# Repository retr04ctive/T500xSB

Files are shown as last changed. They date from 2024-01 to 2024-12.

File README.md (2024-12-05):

# T500xSB Printhead Retroactive Remix

Remix of the T500xVoron mod created by Trist0ne



## Acknowledgements

**Huge thanks for all of the foundation work here:**

 - [T500xVORON](https://github.com/Trist0ne/T500xVORON)

 Follow his method for everything, substuting parts as shown below to fit your needs.

## Features

* Nozzle: [Bambu Hotend](https://www.amazon.com/dp/B0C8JZ788Y/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)
* Thermister and Heater: [Bambu Heater](https://www.amazon.com/dp/B0BW3WXVNR/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)
* Extruder: [Bondtech LGX Lite 2](https://a.co/d/76f52Fn)
* Printhead control board: [BigtreeTech SB2209 RP2040](https://biqu.equipment/products/bigtreetech-ebb-sb2209-can-v1-0)
* Printer control board: [SKR 3 EZ Control Board 32bit](https://www.amazon.com/dp/B0B1WQ9B8L/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)
* Printhead display board: [BigtreeTech KNOMI V2](https://biqu.equipment/products/bigtreetech-knomi-v1-0?_pos=1&_psq=knomi&_ss=e&_v=1.0&variant=40556258459746)
* Buildplate: [WhamBam PEX](https://www.whambamsystems.com/products/flexi-plate-with-pre-installed-pex-build-surface-510-x-510-creality-cr-10-s5_)
* LED Lighting: [RAINBOW BARF LED TOOLHEAD HARNESS FOR STEALTH BURNER](https://kb-3d.com/store/printer-specific-harnesses/566-rainbow-barf-led-toolhead-harness-for-stealth-burner-1653783045189.html)
* Heatbed Mosfet: [MKS MOSFET MOS Module](https://a.co/d/cuV4RM1)

## Modified Printed parts list

**THESE MUST ALL BE PRINTED FROM ABS OR ASA. THEY ARE DESIGNED FOR ABS, I USED ASA. OTHER MATERIALS ARE NOT SUITABLE EITHER DUE TO THEIR TEMPERATURE RESISTANCE OR STRUCTURE CREEP OVER TIME; YOU HAVE BEEN WARNED**

* [STL files](https://github.com/retr04ctive/T500xSB/tree/primary/STL)

## Config file changes

To run this project, you will need to change the Kliper config files to the ones in the config folder above.

I also installed a [Logitech C920 USB Webcam](https://www.logitech.com/en-ch/products/webcams/c920-pro-hd-webcam.960-001055.html) to use with [Obico](https://www.obico.io/) for spaghetti detection.

[Raspberry Pi Pico ADXL](https://klipper.discourse.group/t/raspberry-pi-pico-adxl345-portable-resonance-measurement/1757)

## Recommendations

Follow the [Ellis' Print Tuning Guide](https://ellis3dp.com/Print-Tuning-Guide/articles/index_tuning.html) as well as running the calibrations in [Orca Slicer](https://github.com/SoftFever/OrcaSlicer/wiki/Calibration)

[Sensorless Homing](https://docs.vorondesign.com/community/howto/clee/sensorless_xy_homing.html)

[Klipper PID Tunuing](https://www.obico.io/blog/klipper-pid-tuning/)

[Input Shaping](https://www.klipper3d.org/Measuring_Resonances.html#bed-slinger-printers)

[Perssure Advance](https://github.com/SoftFever/OrcaSlicer/wiki/Calibration)

Slicer Configuration
* Edit your printer settings "Machine G-code" tab as follows:
  * PRINT_START EXTRUDER=[nozzle_temperature_initial_layer] BED=[bed_temperature_initial_layer_single] CHAMBER=[chamber_temperature]
  * PRINT_END

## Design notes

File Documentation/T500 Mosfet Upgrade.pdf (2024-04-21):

## T500 Mosfet Upgrade

I do not recommend doing this unless your warranty has expired

### Prerequisites

Hardware:
Amazon 30a Mosfet https://www.amazon.com/gp/product/B08YZ4W4LN or
Big Red https://www.amazon.com/gp/product/B074KZF772)

STL Files:
1x Mosfet Adapter https://www.thingiverse.com/thing:6375709

Mosfet Install
- Follow this video to remove your mosfet
https://fb.watch/oX4d6himoZ/
- Take the 4 screws from the mosfet and install the Mosfet adapter you printed above
- Take 2 or 4 Screws and install your mosfet to the adapter plate
- Plug the 2 wire control into the board
- Install the 2 wires that come from the PS into the POWER of the New Board (See Diagrams Below)
- Plug to 2 Wires from the Bed Heater into the HOT BED connections (See Diagrams Below)

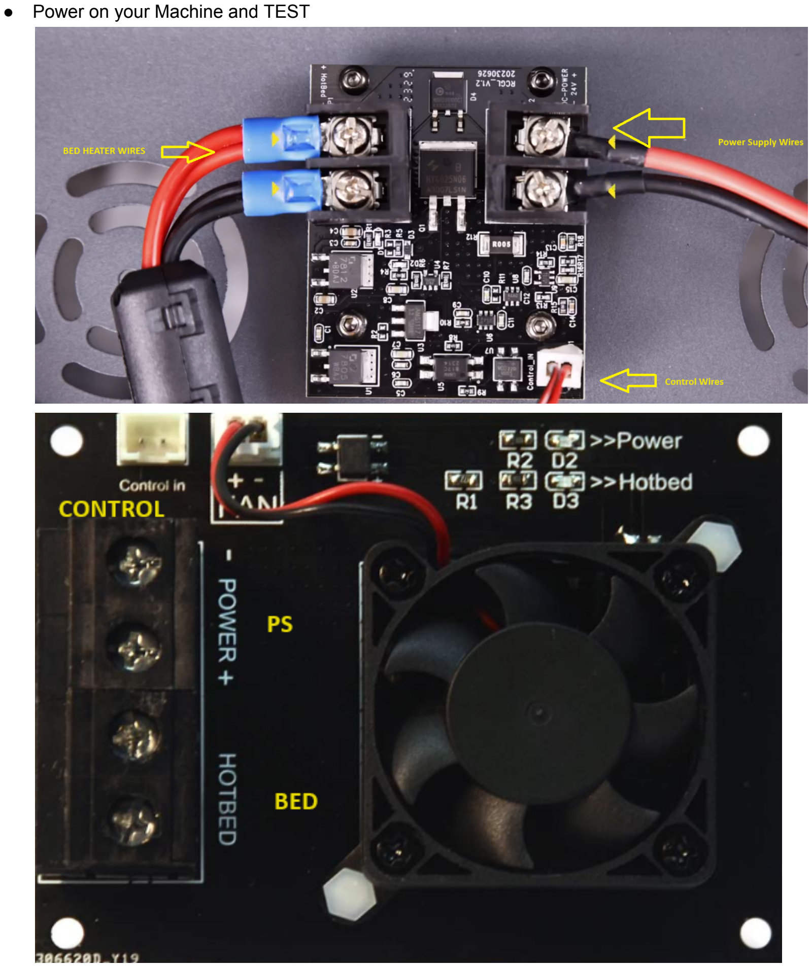
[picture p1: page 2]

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
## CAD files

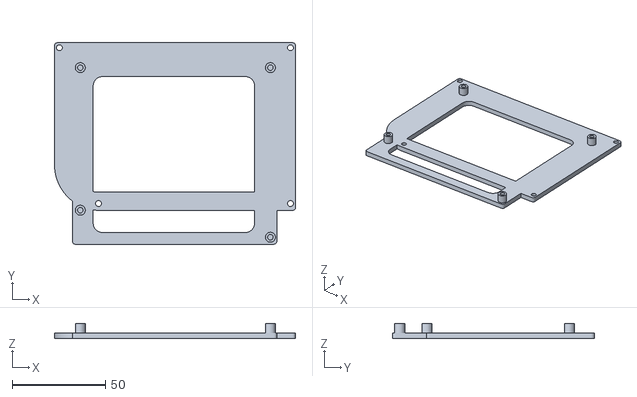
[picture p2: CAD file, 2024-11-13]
STL/SKR T500 Mount.stl
129.3 x 108.1 x 8.00

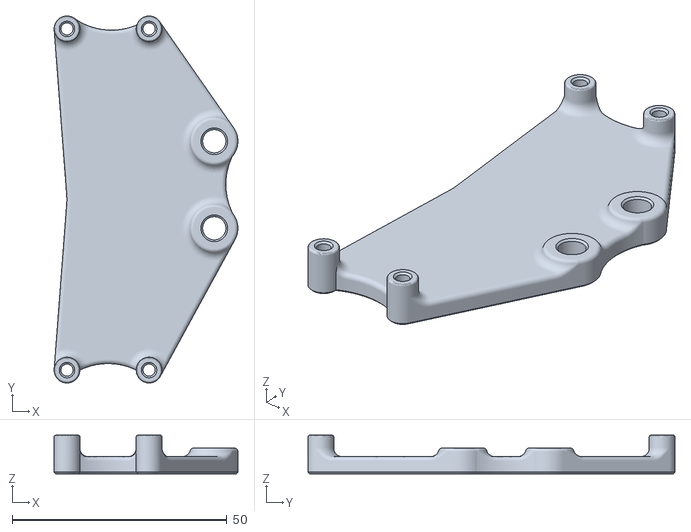
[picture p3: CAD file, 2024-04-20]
STL/BTT U2C Mount.stl
42.8 x 85.4 x 9.00

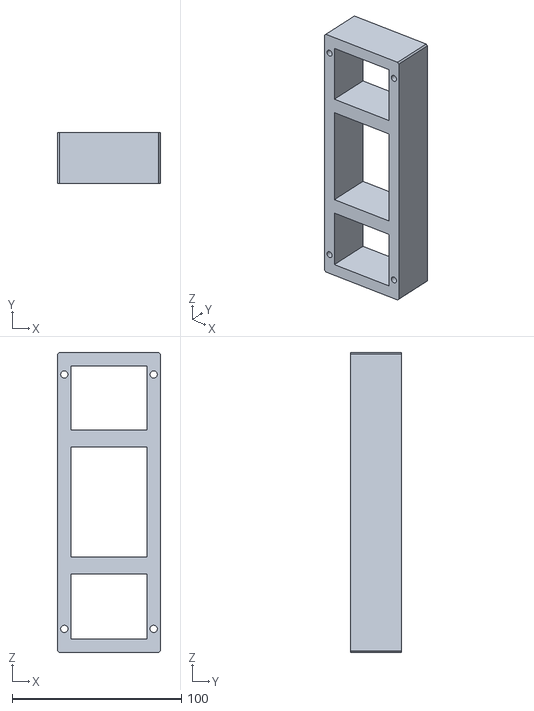
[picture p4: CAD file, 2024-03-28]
STL/Bed Spacer T500 v3.stl
60.9 x 30.0 x 177.5

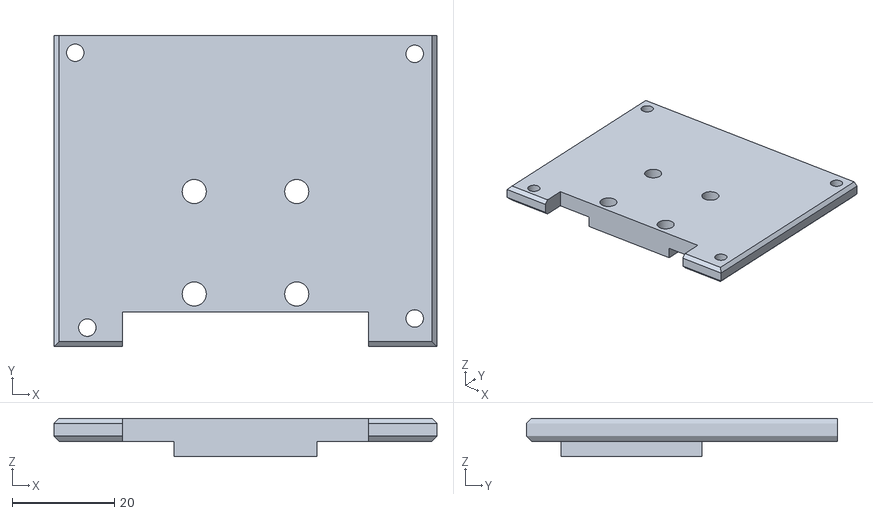
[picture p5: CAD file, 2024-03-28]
STL/Toolhead Adapter Plate.stl
74.8 x 60.7 x 7.50

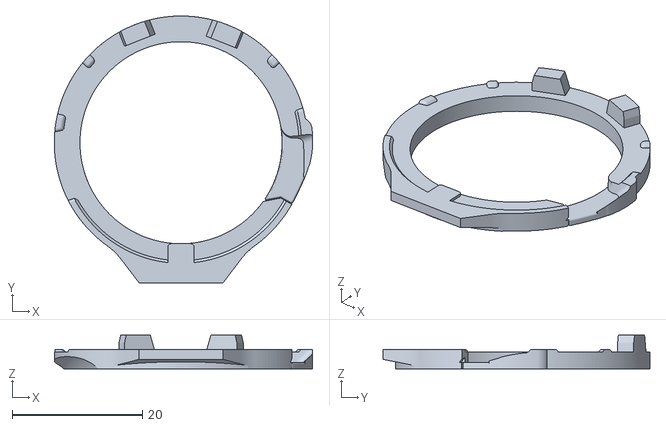
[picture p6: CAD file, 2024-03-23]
STL/KNOMI 2 Mounting Plate.stl
39.7 x 41.0 x 5.20

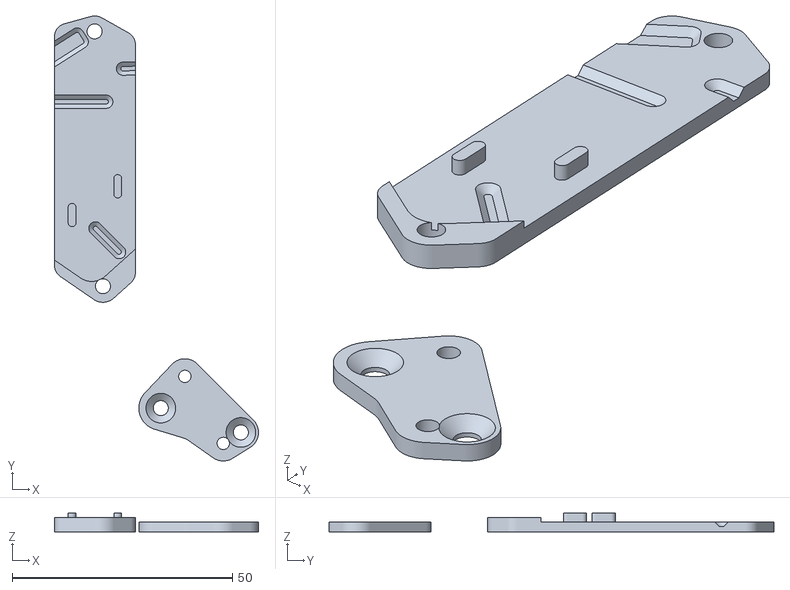
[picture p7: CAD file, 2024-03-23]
STL/ebb_brackets.stl
46.3 x 101.1 x 4.21

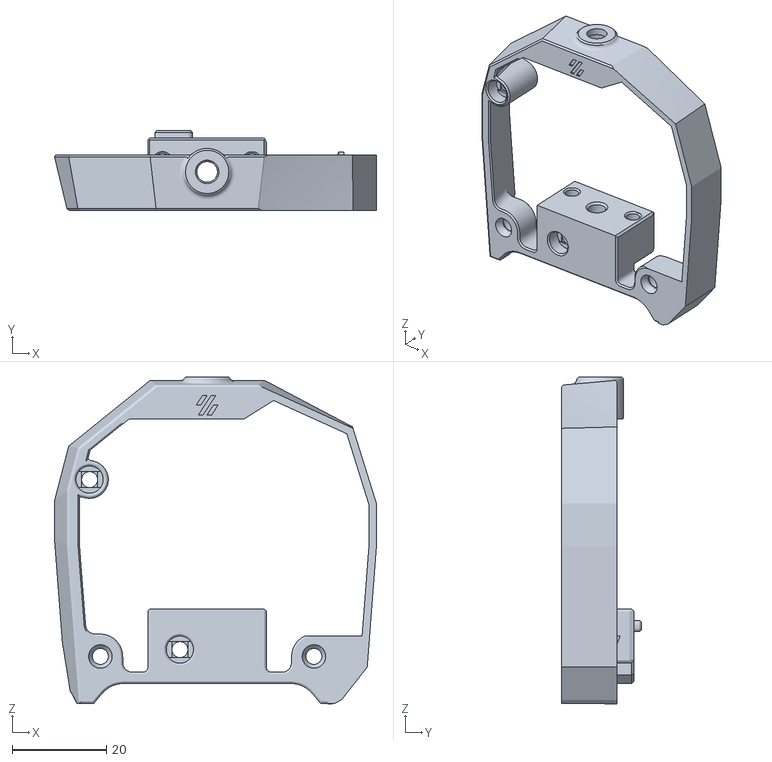
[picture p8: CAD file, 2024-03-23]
STL/LGX_Pro_Front_v1.stl
68.5 x 17.0 x 69.5

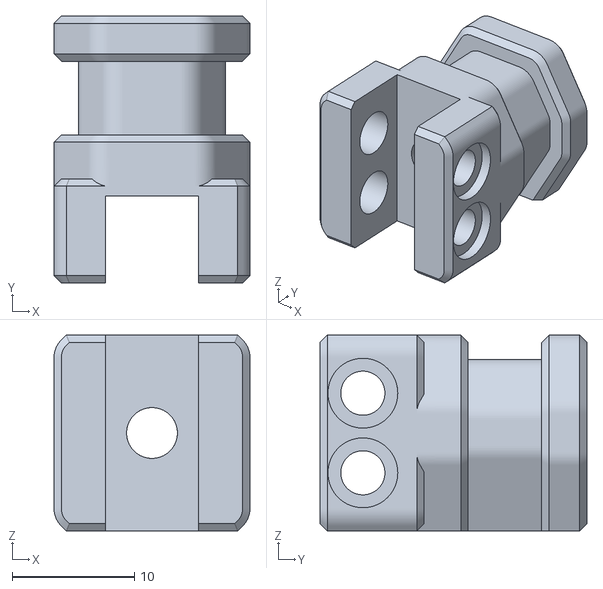
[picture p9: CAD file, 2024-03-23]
STL/SB Bambu Hotend Insert.stl
16.0 x 21.8 x 16.0

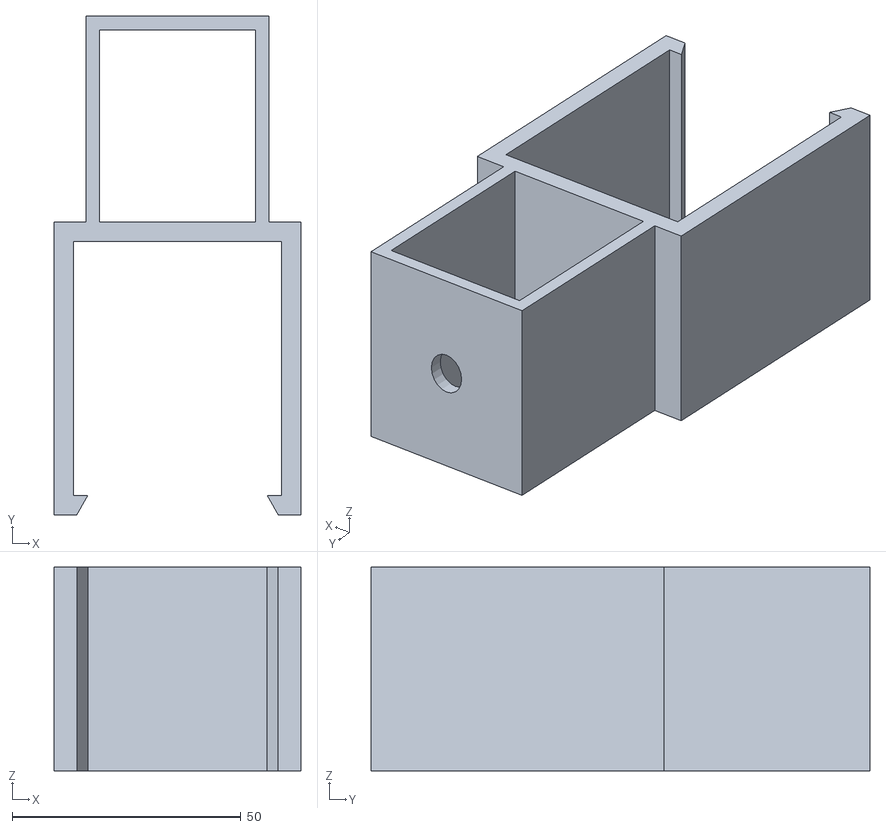
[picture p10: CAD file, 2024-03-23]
STL/Comgrow_t500_cam_mount.stl
54.0 x 109.0 x 44.5

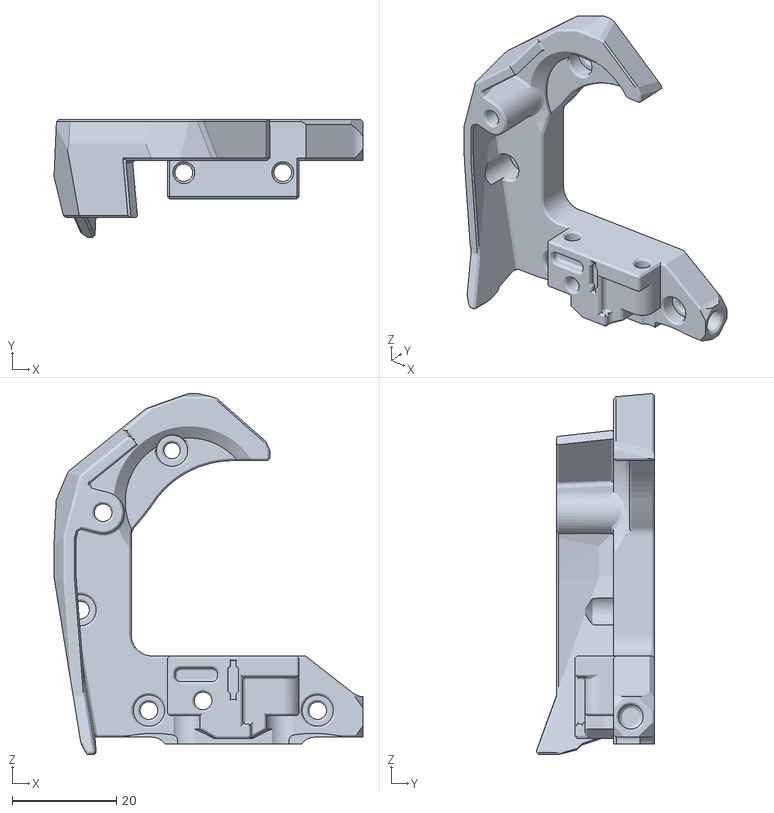
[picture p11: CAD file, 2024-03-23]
STL/LGX_Pro_back_v2.stl
59.3 x 22.6 x 69.3

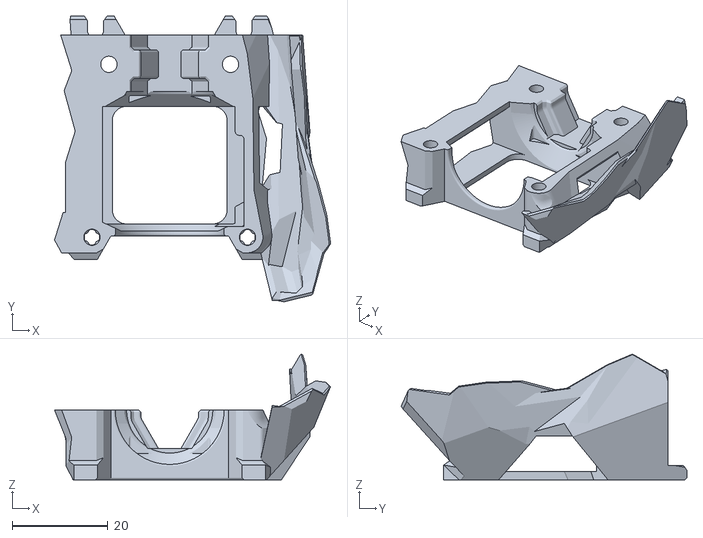
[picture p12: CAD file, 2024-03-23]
STL/SB Bambu Hotend Back.stl
57.7 x 59.7 x 26.3

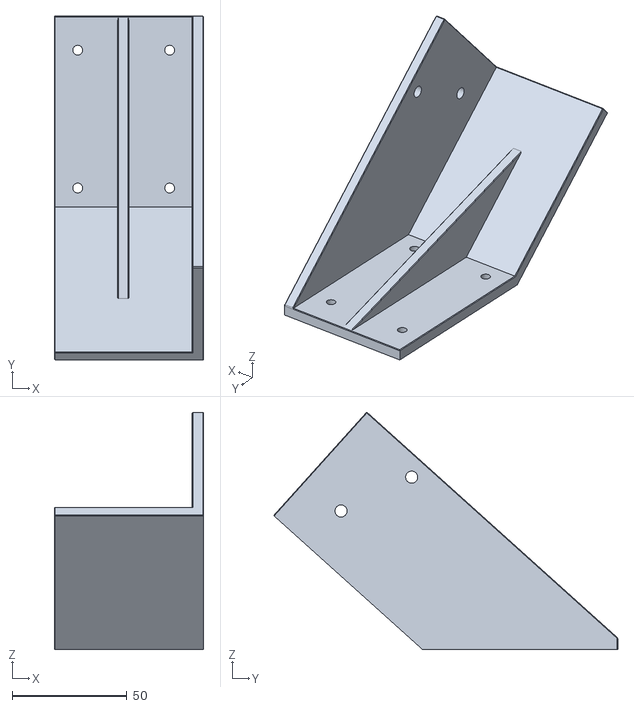
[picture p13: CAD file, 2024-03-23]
STL/Pi TFT70 BTT Case_Bracket_v2.stl
65.0 x 149.6 x 103.1

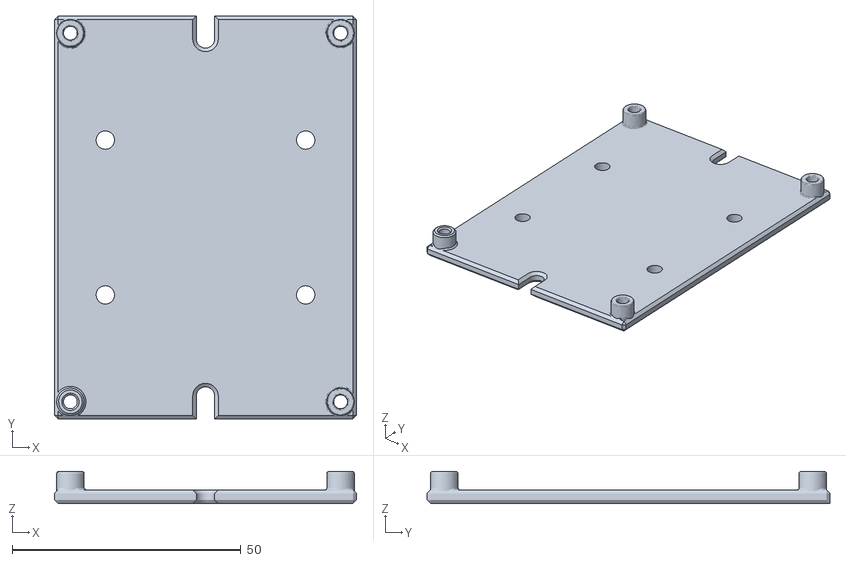
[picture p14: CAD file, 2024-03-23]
STL/T500_MOSFET_ADAPTER_3.stl
66.0 x 88.0 x 7.00

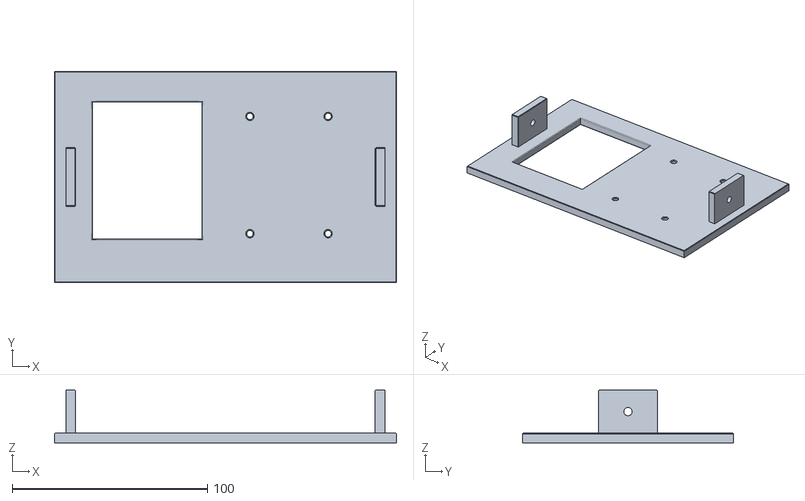
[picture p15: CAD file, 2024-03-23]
STL/Pi TFT70 BTT Case_Back_v4.stl
175.0 x 108.0 x 27.0

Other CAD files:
STL/Comgrow_t500_BTT_SFS_Mount.stl
STL/adxl345_bed_clamp-t500.stl

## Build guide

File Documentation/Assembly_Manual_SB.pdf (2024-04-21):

1

## VORONDESIGN.COM

## VERSION 2023-07-07

# VORON STEALTHBURNER

## We build space shuttles with gardening tools

so anyone can have a space shuttle of their own.

# VORON

2

## VORONDESIGN.COM INTRODUCTION

Before you begin on your journey, a word of caution.

In the comfort of your own home you are about to assemble a robot. This machine can maim, burn, and electrocute you if you are not careful. Please do not become
the first VORON fatality. There is no special Reddit flair for that.

Please, read the entire manual before you start assembly. As you begin wrenching, please check our Discord channels for any tips and questions that may halt your progress.

Most of all, good luck!
THE VORON TEAM

3

## VORONDESIGN.COM TABLE OF CONTENTS

## Introduction

## Hardware

## Overview

## ClockWork2

## Tool Cartridge

## StealthBurner

## X Carriage

## ADXL Mount

## Next Steps

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
## VORONDESIGN.COM INTRODUCTION

PART PRINTING GUIDELINES
The Voron Team has provided the following print guidelines for you to follow in order to have the best chance at success with your parts. There are often questions about substituting materials or changing printing standards, but we recommend you follow these:

3D PRINTING PROCESS
Fused Deposition Modeling (FDM)

MATERIAL
ABS

LAYER HEIGHT
Recommended: 0.2mm

EXTRUSION WIDTH
Recommended: Forced 0.4mm

INFILL TYPE
Grid, Gyroid, Honeycomb, Triangle or Cubic

INFILL PERCENTAGE
Recommended: 40%

WALL COUNT
Recommended: 4

SOLID TOP/BOTTOM LAYERS
Recommended: 5

PRINT IT FORWARD (PIF)
Often times community members that have issues printing ABS will bootstrap themselves into a VORON using our Print It Forward program. This is a service where approved members with VORON printers can make you a functional set of parts to get your own machine up and running. Check Discord if you have any interest in having someone help you out.

5

## VORONDESIGN.COM

HOW TO GET HELP
If you need assistance with your build, we’re here to help. Head on over to our Discord group and post your questions. This is our primary medium to help VORON Users and we have a great community that can help you out if you get stuck.

## https://discord.gg/voron

PRIMARY COLOUR

Example z_joint_lower_x4.stl
These files will have nothing at the start of the filename.

ACCENT COLOUR

Example [a]_tensioner_left.stl
We have added “[a]” to the front of any STL file that is intended to be printed with accent color. The parts are marked with a heart in the manual.

QUANTITY REQUIRED

Example [a]_z_belt_clip_lower_x4.stl
If any file ends with “_x#”, that is telling you the quantity of that part required to build the machine.

FILE NAMING
By this time you should have already downloaded our STL files from the Voron GitHub. You might have noticed that we have used a unique naming convention for the files. This is how to use them.

## INTRODUCTION

CLEAR/TRANSPARENT

Example [c]_led_diffuser.stl
We have added “[c]” to the front of any STL file that is intended to be printed with clear or transparent filament (cloudy is better than clear; white or light grey may also work in a pinch).

OPAQUE

Example [o]_led_diffuser_mask.stl
We have added “[o]” to the front of any STL file that is intended to be printed with an opaque filament (blocks light, dark colours and blacks).

6

## VORONDESIGN.COM INTRODUCTION

THIS IS JUST A REFERENCE
This manual is designed to be a simple reference manual. Building a Voron can be a complex endeavour and for that reason we recommend downloading the CAD files off our Github repository if there are sections you need clarification on. It can sometimes be easier to follow along when you have the
whole assembly in front of you.

## https://github.com/vorondesign

## https://docs.vorondesign.com

REPORTING ISSUES
Should you find an issue in the documentation or have a suggestion for an improvement please consider opening an issue on GitHub (https://github.com/VoronDesign/Voron-Stealthburner/issues). When raising an issue please include the relevant page numbers and a short description; annotated screenshots are also very welcome. We periodically update the manual based on the feedback we get.

# DOCS (https://docs.vorondesign.com/)

7

## VORONDESIGN.COM

BUTTON HEAD CAP SCREW (BHCS) Metric fastener with a domed shape head and hex drive. Most commonly found in locations where M5 fasteners are used.

ISO 7380-1

SOCKET HEAD CAP SCREW (SHCS) Metric fastener with a cylindrical head and hex drive. The most common fastener used on the Voron.

ISO 4762

## HARDWARE REFERENCE

SELF TAPPING SCREW
Fastener with a pronounced thread profile that is screwed directly into plastic.

HEAT SET INSERT
Heat inserts with a soldering tip so that

they melt the plastic when installed. As the plastic cools, it solidifies around the knurls and ridges on the insert for excellent resistance to both torque and pull-out.

WASHER
Usually stamped from sheet metal this

type of spacer is not as consistent in thickness as the shims are. Only used in M3 size.

DIN 125

SET SCREW
Small headless screw with an internal drive. Used in pulleys and other gears. Also called a grub screw.

ISO 4026

HEX NUT
Hex nuts couple with bolts to create a tight, secure joint.

ISO 4032

FLAT HEAD CAP SCREW (FHCS) Metric fastener with a flat head and hex drive.
ISO 10642

8

## VORONDESIGN.COM

## VORONDESIGN.COM

## OVERVIEW

9

Voron StealthBurner

Voron ClockWork2 Extruder

Voron StealthBurner Tool Cartridge

ADXL Sensor Mount

10

VORON CLOCKWORK2 | VORONDESIGN.COM

11

## VORONDESIGN.COM

Heat Set Insert

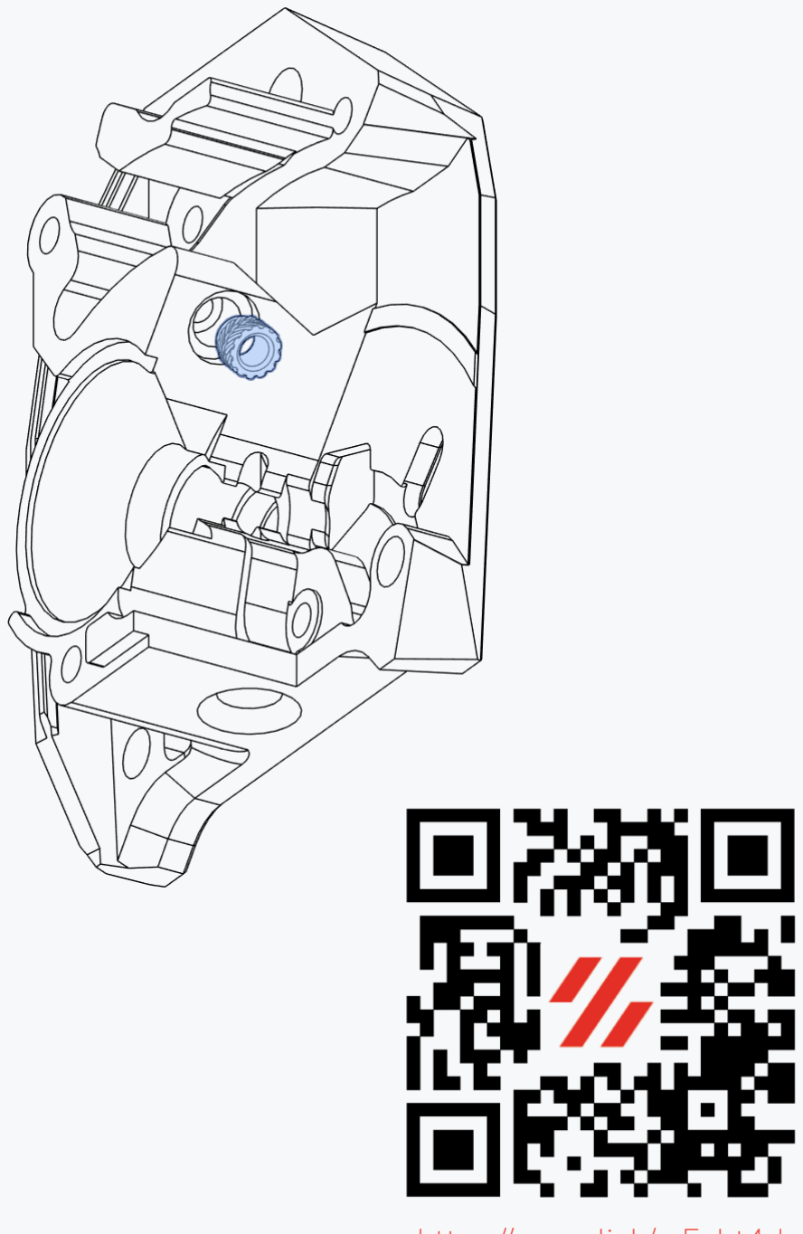
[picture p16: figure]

https://voron.link/m5ybt4d

HEAT SET INSERTS
This design relies heavily on heat set inserts. Make sure you have the proper inserts (check the hardware reference for a close-up picture and the Sourcing Guide (https://vorondesign.com/sourcing_guide) for dimensions).

If you’ve never worked with heat set inserts before we recommend you watch the linked guide.

## HEAT SET INSERTS

## VORONDESIGN.COM

## HEAT SET INSERTS

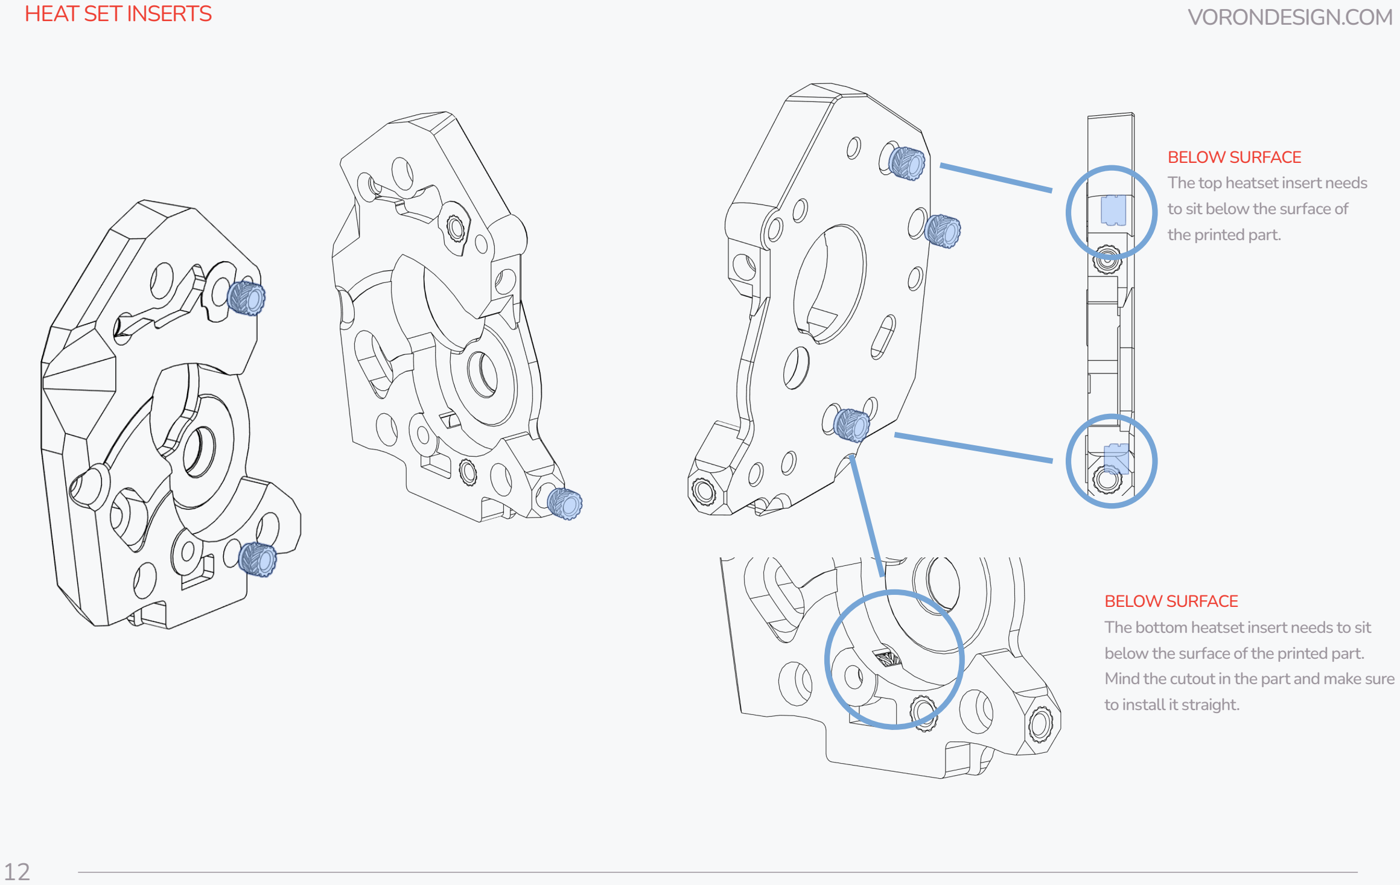
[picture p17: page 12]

12

BELOW SURFACE
The bottom heatset insert needs to sit below the surface of the printed part. Mind the cutout in the part and make sure to install it straight.

BELOW SURFACE
The top heatset insert needs to sit below the surface of the printed part.

13

## VORONDESIGN.COM

OPTION: TOOLHEAD PCB
If you opt to use a toolhead PCB, add additional heat set inserts into locations highlighted below.

Heat Set Insert

## HEAT SET INSERTS

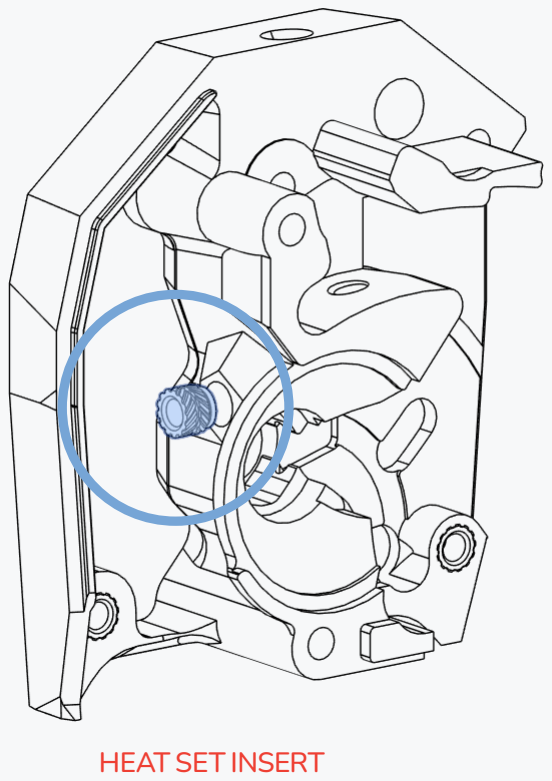
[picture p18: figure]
HEAT SET INSERT

Be careful when inserting this heat set insert. It’s easy to accidentally touch the left side of the part with the soldering iron.

14

## VORONDESIGN.COM

GENERIC CABLE CHAINS
The 3-hole pattern is usually found on generic cable chains.

IGUS CABLE CHAINS
IGUS chains have 2 mounting holes.

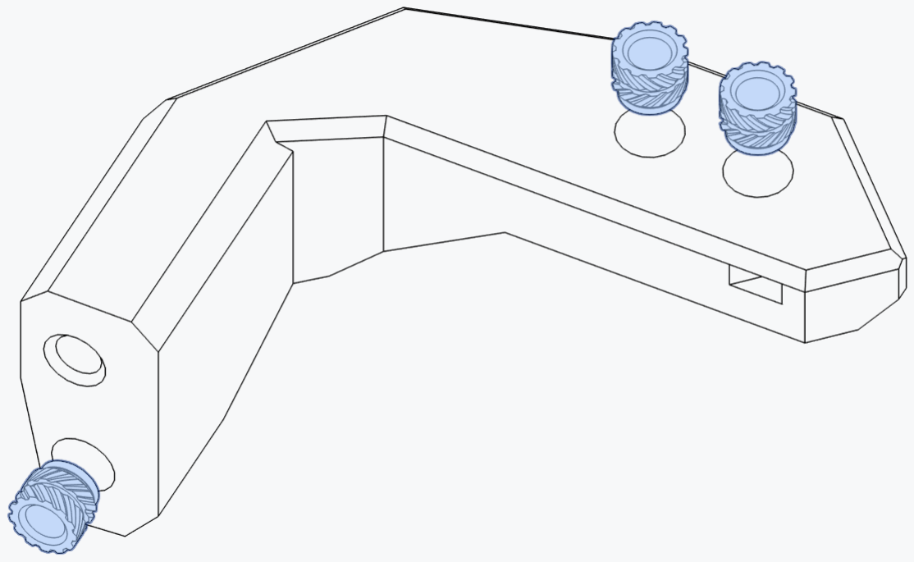
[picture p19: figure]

Heat Set Insert

## HEAT SET INSERTS

PRINTER SPECIFIC MOUNTS
V2, Trident and Legacy use the same printed parts. Extra parts are included for SwitchWire.

15

HEAT SET INSERTS | VORONDESIGN.COM

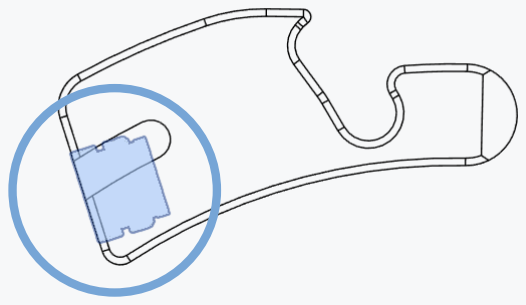
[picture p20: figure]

FLUSH WITH SURFACE
The heatset insert needs to sit flush or slightly below the surface of the printed part.

ACCENT PART?
Look for Voron heart next to the part. It indicates that this is a part that is usually printed in the accent color.

16

GUIDLER ARM | VORONDESIGN.COM

GUIDLER ARM | VORONDESIGN.COM

17

BMG Idler Assembly

LUBRICATE BEARINGS
A lubrication film is required to ensure smooth operation and longevity.
Refer to the Voron sourcing guide (https://vorondesign.com/sourcing_guide) for lubricant options - look for a “light grease”.

MIND ORIENTATION
Make sure to orient the idler assembly as shown above.

## VORONDESIGN.COM

## GUIDLER ARM

18

BMG Thumbscrew Assembly

A NOTE ON SPRINGS
Longer/shorter/stiffer springs will change the tension characteristics and have an impact on how well the tension mechanism works. Consider buying the original Bondtech part (https://www.bondtech.se/product/thumbscrew-assembly/) as those are known to work well. If sourced from a different vendor check if it’s roughly 12mm long with an outer diameter of 6mm and a wire thickness of 1mm.

19

## VORONDESIGN.COM

MR85 Bearing

## MOTOR PLATE

BEARING FIT

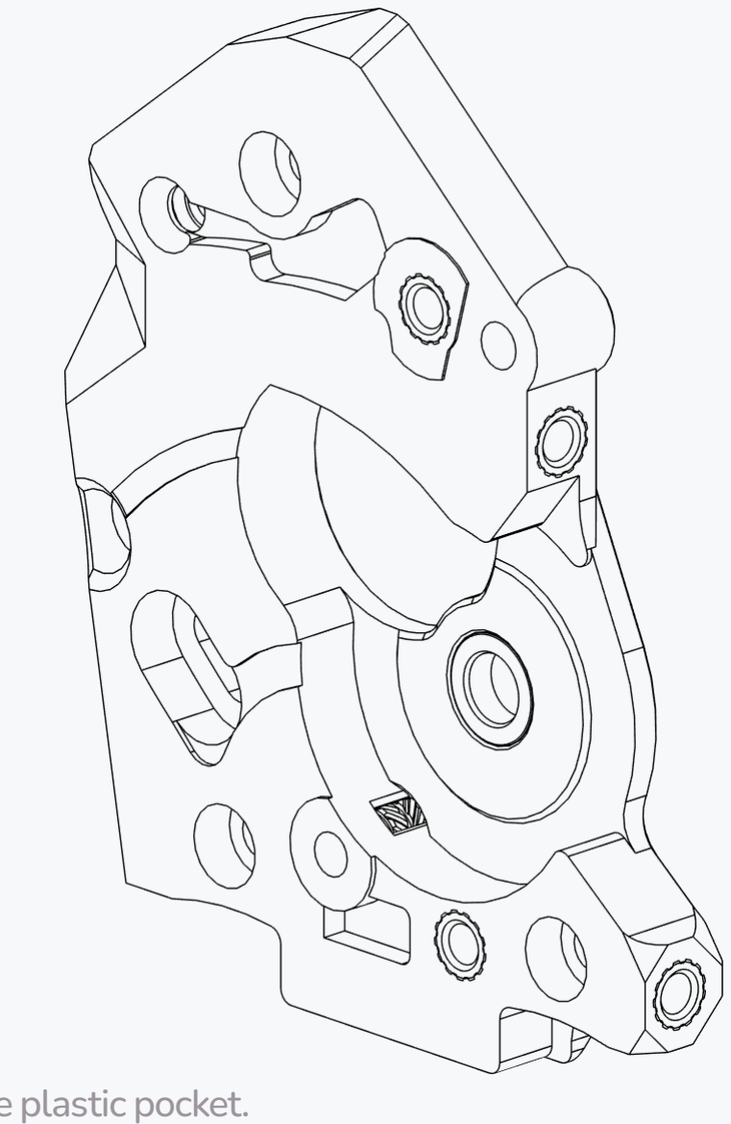
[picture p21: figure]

Fully seat the bearing into the plastic pocket. Apply even pressure to insert them. Avoid pressing on the inner ring of the bearing.

If the fit is too tight the printed parts are likely over-extruded.

MR85 Bearing

CHECK BEARING FIT
The bearings must slip on and off the shaft easily to allow the gear to self-centre.

Pressing the bearings on the shaft will damage them.

Lightly sand the shaft if required.

20

## VORONDESIGN.COM

MR85 Bearing

## MAIN BODY

M3x6 FHCS

BEARING FIT
Fully seat the bearing into the plastic pocket. Apply even pressure to insert them. Avoid pressing on the inner ring of the bearing.

THREAD LOCKER PLEASE
Adding a small amount of medium strength thread locker to this flat head screw will keep it from coming loose over time.

21

## VORONDESIGN.COM

DRIVE GEAR
Make sure the set screw in the filament drive gear is seated against the notch in the shaft. Carefully tighten the set screw, the head is easy to strip.

## DRIVE ASSEMBLY

A NOTE ON GEARS
Poorly made gears often cause print quality issues. For best performance consider

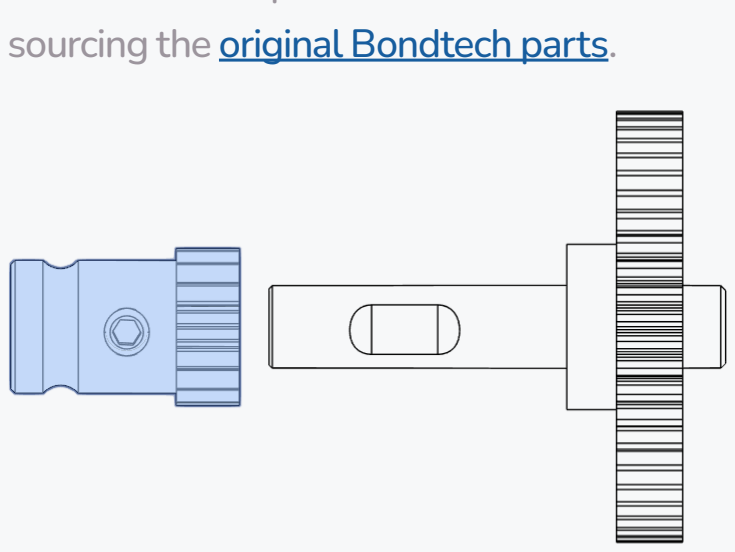
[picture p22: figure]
sourcing the original Bondtech parts.

INITIAL POSITION

The final position is set later.

The final position of the drive gear is set in a later step. Common thread lockers have a long enough working time to complete the steps without issues.

Familiarize yourself with the steps on the next 3 pages before you apply thread locker.

Complete the steps on the next 3 pages after applying the thread locker.

22

MAIN BODY | VORONDESIGN.COM

23

## VORONDESIGN.COM

M3x25 SHCS

INITIAL ALIGNMENT CHECK
Check if the filament path aligns with the toothed section of the drive gear.

## MAIN BODY

Tighten until the plastic bends and cracks. Back up 2 turns, discard parts, reprint and try again.

24

## VORONDESIGN.COM

CHECK FOR CLEARANCE
The drive shaft must not touch the motor housing. Make sure it does not sit above the surface of the printed part.

Check if the shaft has sufficient clearance when fully seated.

Depending on the shafts tolerances you may need to adjust the position of the drive gear or sand the face of shaft.

CHECK ALIGNMENT
With the filament inserted, verify if the filament path and drive gear are aligned.

Loosen the set screw and adjust the position of the drive gear if required.

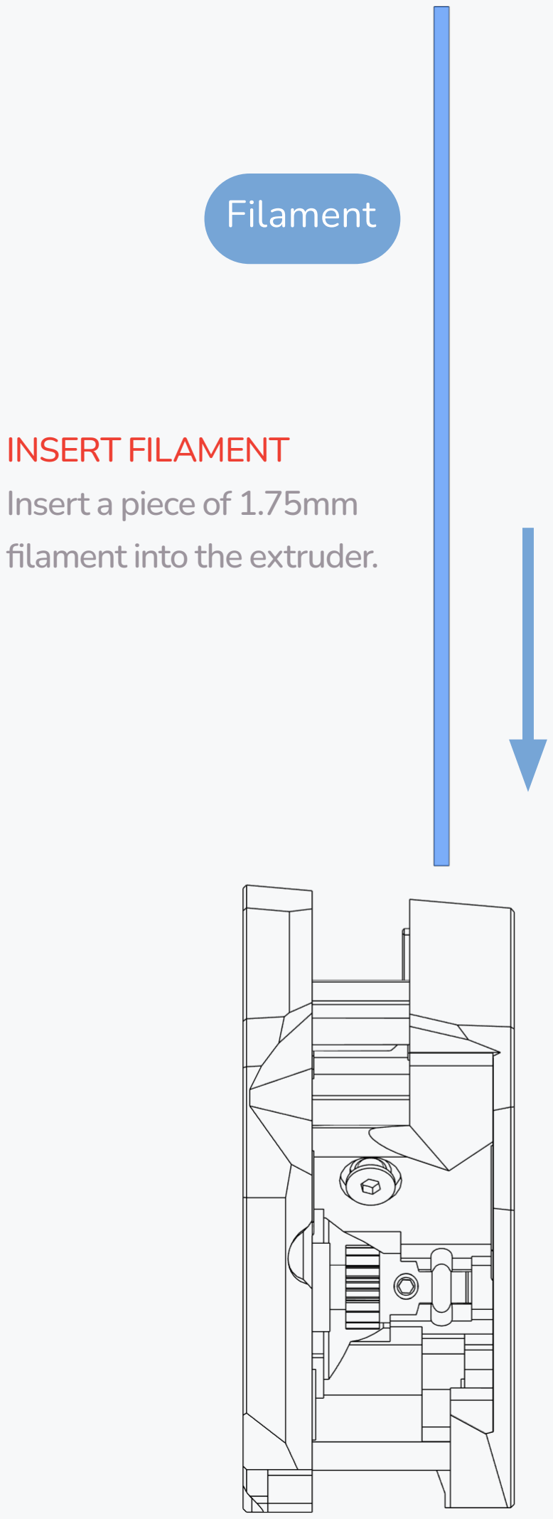
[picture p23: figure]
Insert a piece of 1.75mm filament into the extruder.; Filament

INSERT FILAMENT

## DRIVE ALIGNMENT

TENSION ARM | VORONDESIGN.COM

25

M3x25 SHCS

DON’T TIGHTEN
The tensioning arm must move freely. Tightening the bolt may lock it in place.

26

## VORONDESIGN.COM

M3x25 SHCS

## LATCH

27

TENSION MECHANSIM | VORONDESIGN.COM

TENSION KNOB
Turning the thumb screw clockwise will increase the tension and grip on the filament. Too much tension will result in print issues.

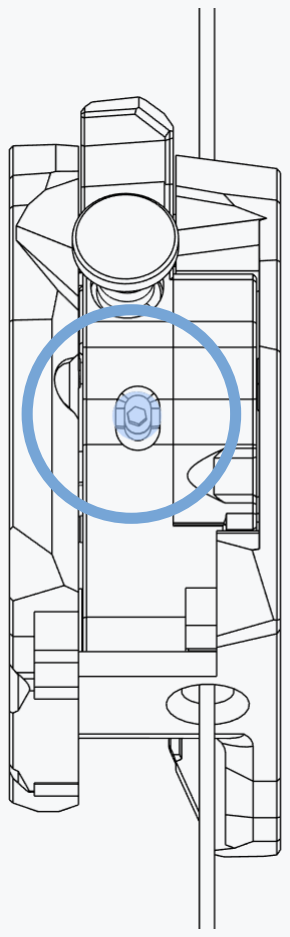
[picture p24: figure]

ANTI SQUISH THINGYMAJIG
Softer and flexible materials will deform
and extrude poorly under too much tension. ClockWork2 adds an adjustment feature to set the minimum distance between the drive gear and the idler, limiting the squish on the filament, and to prevent the gears from meshing too tightly or binding up the extruder.

## VORONDESIGN.COM

## STEPPER MOTOR

28

M3x30 SHCS

NEMA14 Stepper

29

## VORONDESIGN.COM

M3x8 SHCS

ACCESS HOLE

The second motor bolt can
be accessed from the front of the extruder.

## STEPPER MOTOR

The motor position will be adjusted in the next steps. Don’t fully tighten just yet.

30

## VORONDESIGN.COM

CHECK GEAR PLAY
The gear should have a slight play and should not be fully tight against the pinion. Adjust the position of the motor until you have a faint play.

SET GEAR MESHING
Adjust the stepper motor position so that the motor and extruder gear teeth fully mesh /overlap with each other. There should be a very small gap between the faces of the gear teeth; the gears must not press tightly against each other.

## STEPPER MOTOR

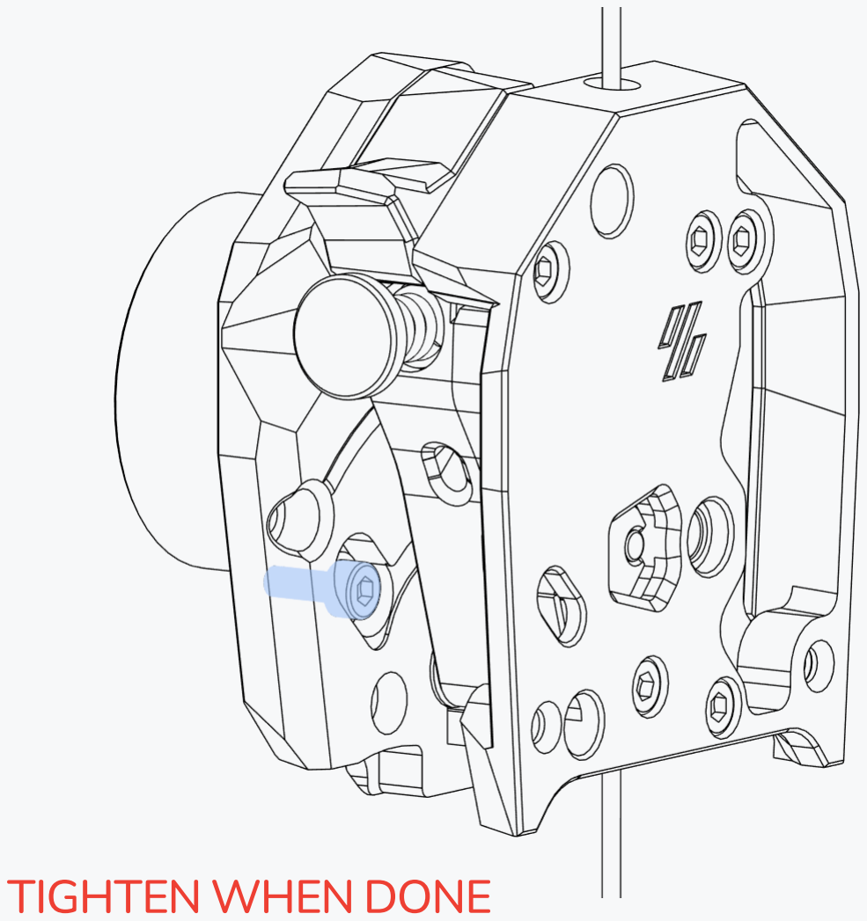
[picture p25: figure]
TIGHTEN WHEN DONE

Don’t forget to tighten the second motor bolt after adjusting.

https://voron.link/u6ehxsw

31

CHAIN ANCHOR | VORONDESIGN.COM

32

CABLE BRIDGE | VORONDESIGN.COM

M3x8 SHCS

CABLE COVER | VORONDESIGN.COM

33

M3x16 SHCS

OPEN LATCH
Undo the filament latch to expose the bolt pocket for the cable cover.

## VORONDESIGN.COM

## CABLE COVER

34

ACCESS HOLE
The bolt drive can be accessed from the front of the extruder.

DON’T OVER-TIGHTEN
The bolt is threaded directly into plastic.

M3x6 BHCS

35

## VORONDESIGN.COM

StealthBurner development started on 2021-04-13 with a simple: “I’m going to regret saying this but, ‘How hard could it be?’”

36

## VORONDESIGN.COM

37

## VORONDESIGN.COM

IDENTIFYING PRINTED PARTS
The hotend type is embossed on the printed parts.

Make sure they match your hotend.

AVAILABLE MOUNTS

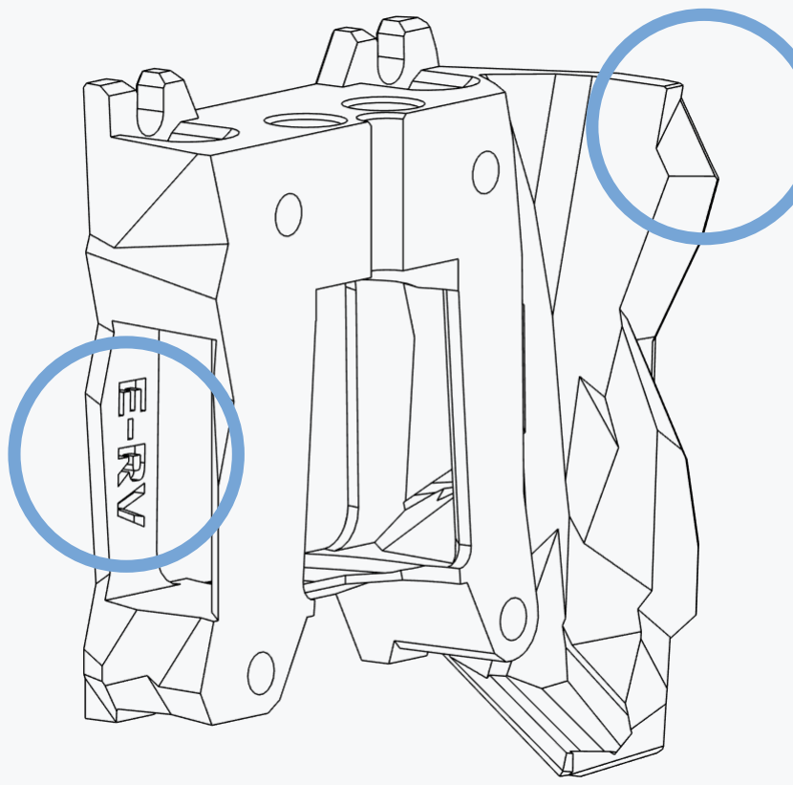
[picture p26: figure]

We also provide mounts for other hotends. They are assembled in a similar manner.

For a full list of available mounts and their identification code, see the readme file included in the toolheads folder.

## PART MARKINGS

MISSING CORNER? CW1? CW2?
We also provide tool cartridge parts for ClockWork1, and other extruders designed as an alternative to CW1. They are identical except for an opening in the highlighted corner to help with wire routing for those designs.

38

## VORONDESIGN.COM

OPTION: ADXL PCB MOUNT
To use the optional ADXL PCB for Klipper’s Input Shaper calibration, add additional heat set inserts into the holes in highlighted location.

Heat Set Insert

## PART PREP

39

## VORONDESIGN.COM

Revo Nozzle

Revo HeaterCore

Revo Voron Heatsink

## PART PREP

40

PART PREP | VORONDESIGN.COM

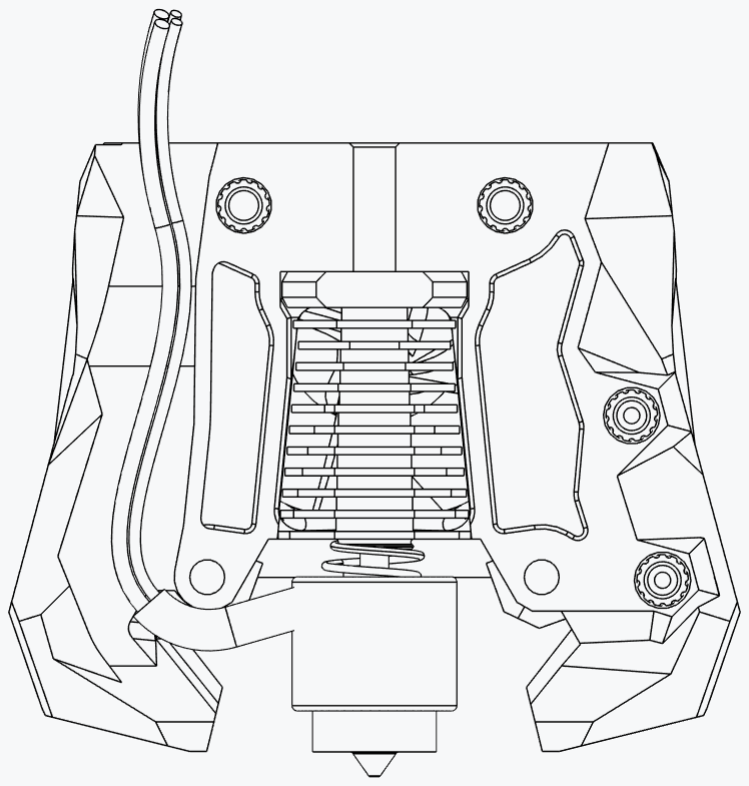
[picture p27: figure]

BEND STRAIN RELIEF
Carefully bend the strain relief to clear the printed part. Firmly hold the HeaterCore to prevent bending the Revo Nozzle.

It is critical that the Revo Nozzle is fully hand tightened into the heatsink. You MUST bend the strain relief to achieve this.

HOTEND WIRE ROUTING
Route the wires as shown to the right. This is universal to all hotend types.

41

## VORONDESIGN.COM

M3x16 SHCS

## TOOL CARTRIDGE

42

## VORONDESIGN.COM

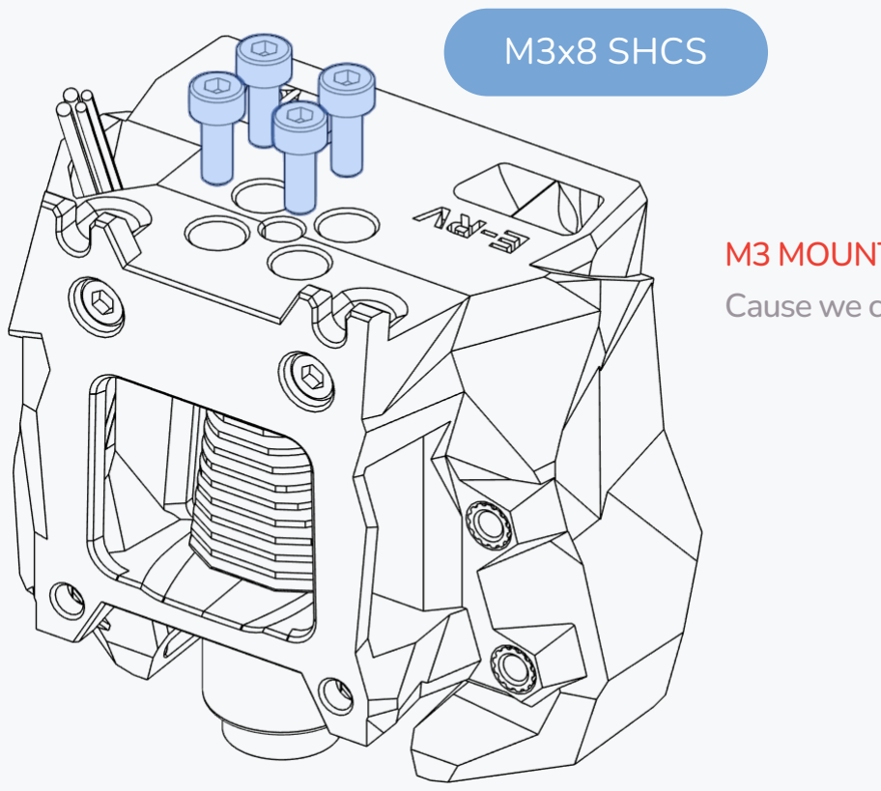
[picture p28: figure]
M3x8 SHCS

M3 MOUNTING BOLTS?
Cause we can, that’s why.

## TOOL CARTRIDGE

43

## VORONDESIGN.COM

PTFE STICKOUT
The PTFE tube should stick out 11mm above the surface of the printed part.

The stick out length might vary if you use an extruder other than the ClockWork2.

## TOOL CARTRIDGE

44

## VORONDESIGN.COM

45

## VORONDESIGN.COM

Remove built-in supports (highlighted in

## SUPPORTS

## VORONDESIGN.COM

46

DOUT

DOUT

DOUT
DIN

DIN

DIN | DIN

### DOUT

5V

GND

5V

5V

GND

GND

To Controller Board

+ -

120mm 3x 0.16mm²(AWG26-30)

100mm 3x 0.16mm²(AWG26-30)

LOGO LED
Index=1

TOOLHEAD LED RIGHT
Index=2

TOOLHEAD LED LEFT
Index=3

100mm 3x 0.16mm²(AWG26-30)

### DIN

### DOUT

5V

GND

### DIN

### DOUT

5V

GND

To Controller Board

LED WIRING
Connect the “OUT” side of the LED to the “IN” side of the next LED in the chain.

Solder the wires as shown on the right. Both the “IN” and the “OUT” wires must exit in the same direction in order to fit into the printed parts.

For Illustration Only, Read “LED Wiring” Callout

47

LEDS | VORONDESIGN.COM

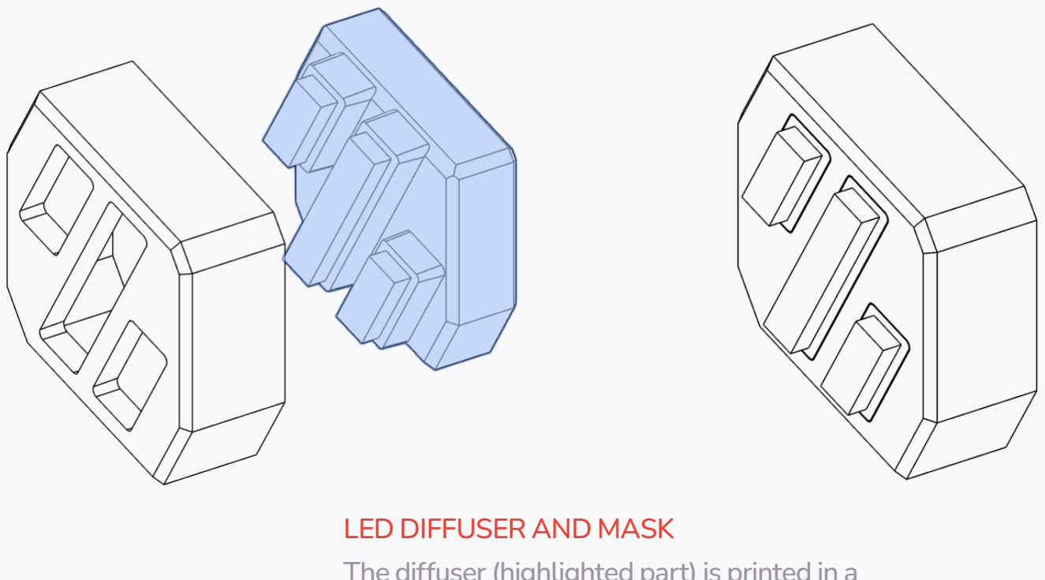
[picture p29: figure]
LED DIFFUSER AND MASK

The diffuser (highlighted part) is printed in a translucent filament to evenly spread the light.

The mask (part to the left) is printed in an opaque filament to prevent the light from leaking, resulting in a crisp logo.

48

LEDS | VORONDESIGN.COM
TOOLHEAD LED LEFT | TOOLHEAD LED RIGHT

49

LEDS | VORONDESIGN.COM

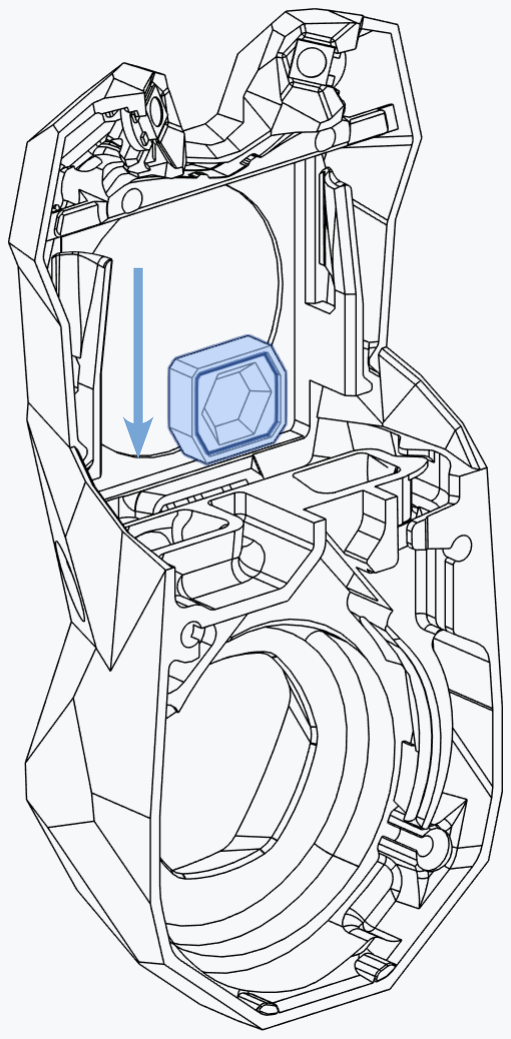
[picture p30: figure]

DIFFUSER INSERTION
Insert the printed parts and push them towards the front.

50

LEDS | VORONDESIGN.COM

51

## VORONDESIGN.COM

## LEDS

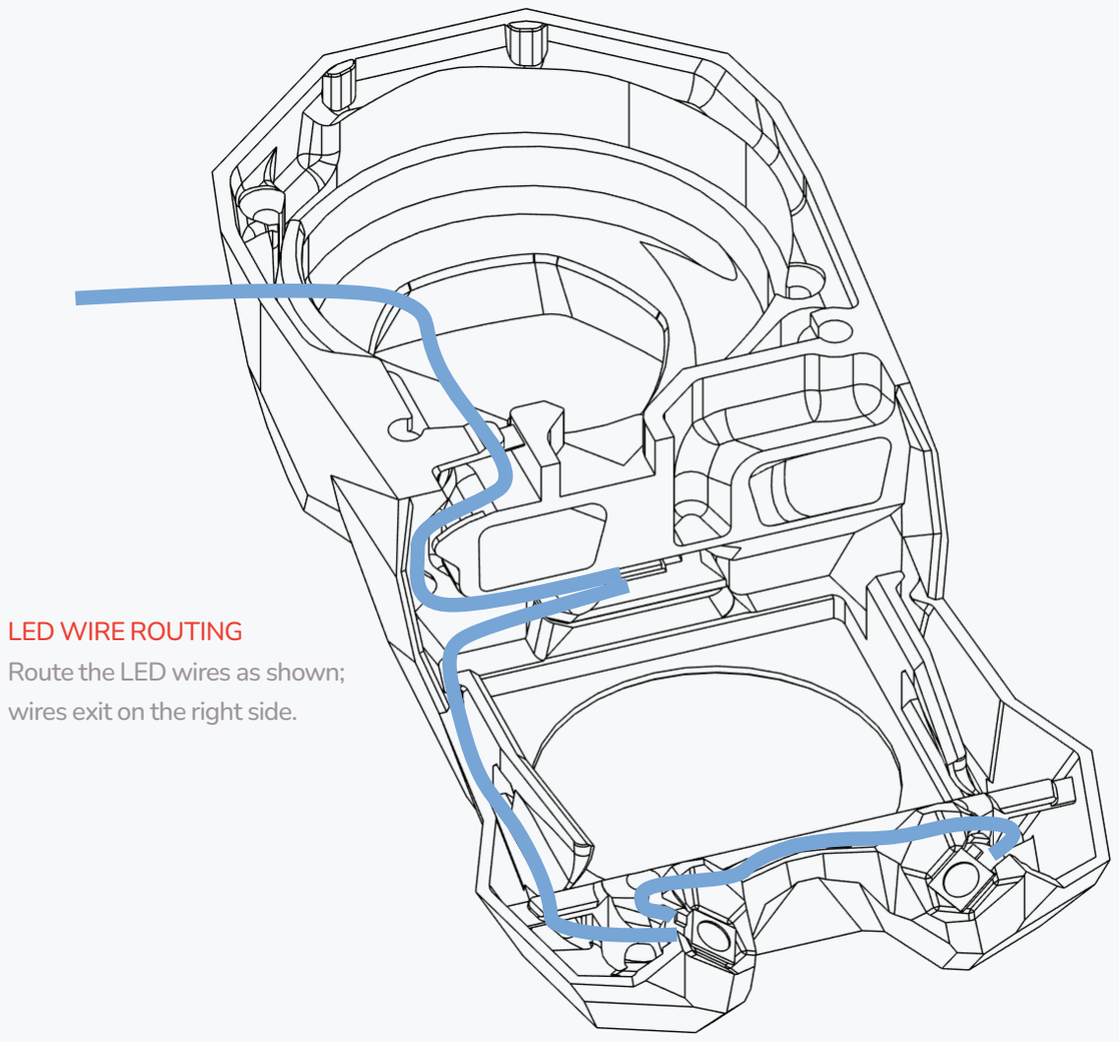
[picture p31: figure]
LED WIRE ROUTING Route the LED wires as shown; wires exit on the right side.

52

## VORONDESIGN.COM

The highlighted parts are build-in support

during the fan installation.

## SUPPORTS

53

## VORONDESIGN.COM

Rotate the fan so that the wires exit on the top and the air is pushed “inwards”.

## HOTEND FAN

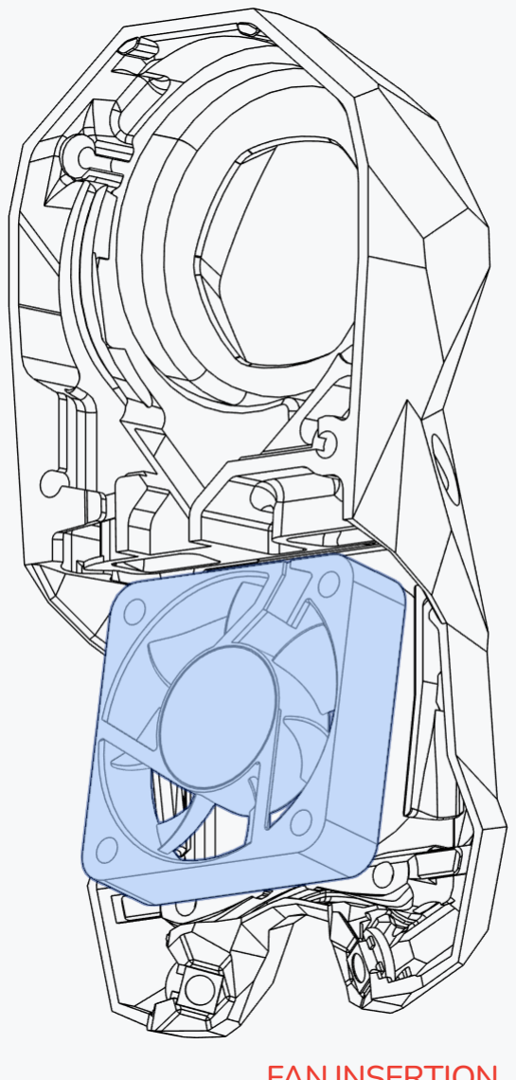
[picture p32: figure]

FAN INSERTION

Insert the fan at a slight angle and clip it into place.

Mind the fan orientation.

54

HOTEND FAN | VORONDESIGN.COM

FAN WIRE ROUTING

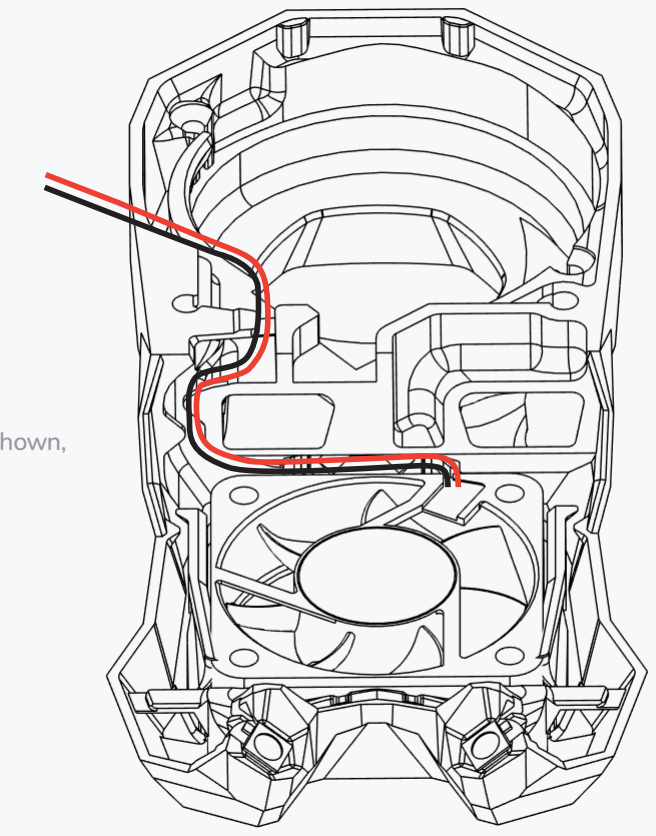
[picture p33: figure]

Route the fan wires as shown, exiting on the right side

55

## VORONDESIGN.COM

FAN PREPARATION
Remove the front of the 5015 fan. Clip off and file down the stock mounting ears.

There’s a trimming jig STL included in the release to make this task easier.

## PART COOLING FAN

56

PART COOLING FAN | VORONDESIGN.COM

M3x6 FHCS

57

## VORONDESIGN.COM

Yeah, it went about as expected.

58

X CARRIAGE | VORONDESIGN.COM

59

## VORONDESIGN.COM

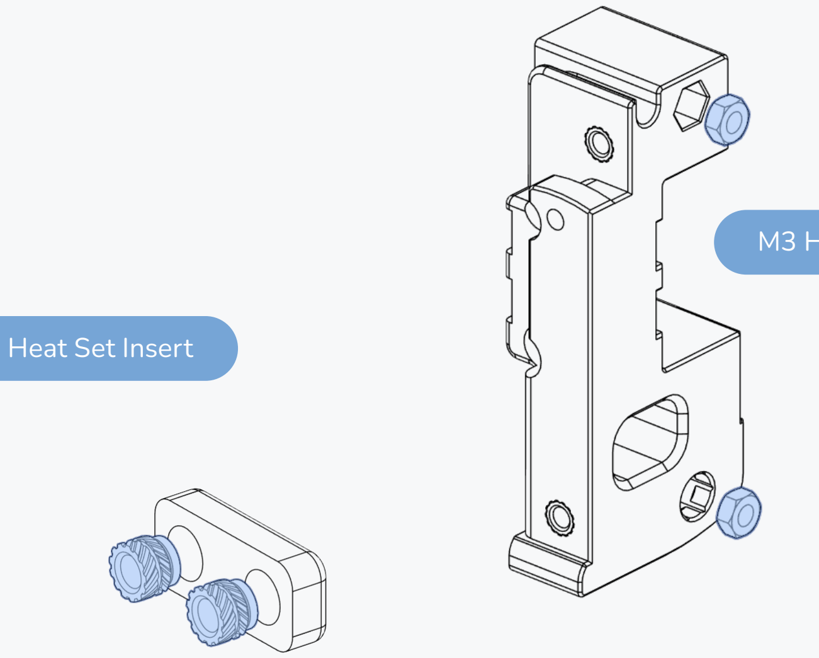
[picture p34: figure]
Heat Set Insert

M3 Hex Nut

## PART PREP

We provide different versions of the carriage to fit our different printer designs. Be sure to pick the right one for your printer. the next few pages may look slightly different if you are building a Switchwire printer.

60

## VORONDESIGN.COM

## X CARRIAGE

FOLLOW BELTING AND X CARRIAGE INSTALLATION OUTLINED IN PRINTER MANUAL Consult the printer’s manual for instructions on how to run the belts and details on carriage mounting.

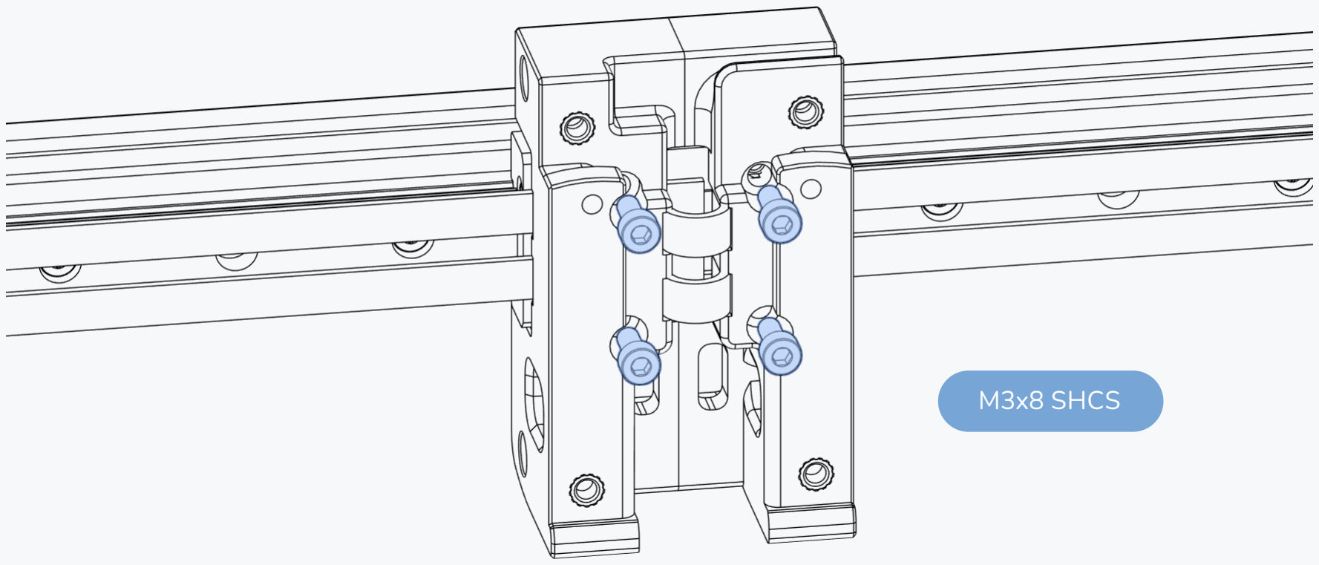
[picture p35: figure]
M3x8 SHCS

## VORONDESIGN.COM

## X CARRIAGE

61

M3x30 SHCS

M3x30 SHCS

M3x12 SHCS

30MM OR 40MM?
the length of these two bolts can be different based on the specific printer you are building. This step has some overlap with the printer manuals. please refer to the printer psecific manual for the correct bolt lengths

## VORONDESIGN.COM

## X CARRIAGE

62

Omron Style Probe | M3x30 SHCS

OTHER PROBE TYPES
The picture shows the
recommended Omron
TL-Q5MC probe.

Other probes with a similar form factor and characteristics might work as well.

63

## VORONDESIGN.COM

The position can be fine-tuned later. Set an initial position of about 6mm below the plastic part.

## X CARRIAGE

## VORONDESIGN.COM

## CW2 MOUNTING

64

M3x8 SHCS

65

## VORONDESIGN.COM

## CW2 MOUNTING

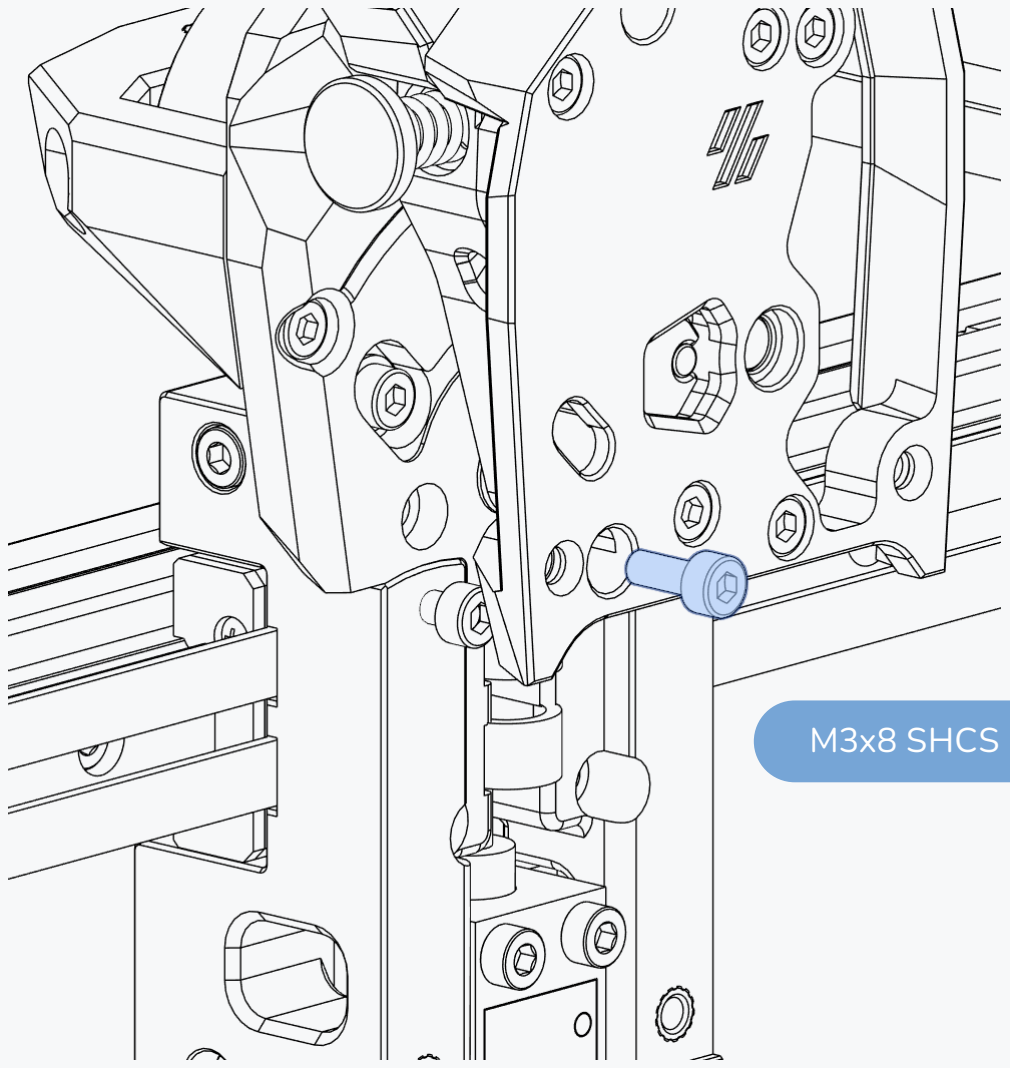
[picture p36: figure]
M3x8 SHCS

ACCESS HOLE

The bolt can be accessed from the front of the extruder.

66

TOOL CARTRIDGE MOUNTING | VORONDESIGN.COM

## VORONDESIGN.COM

## SB MOUNTING

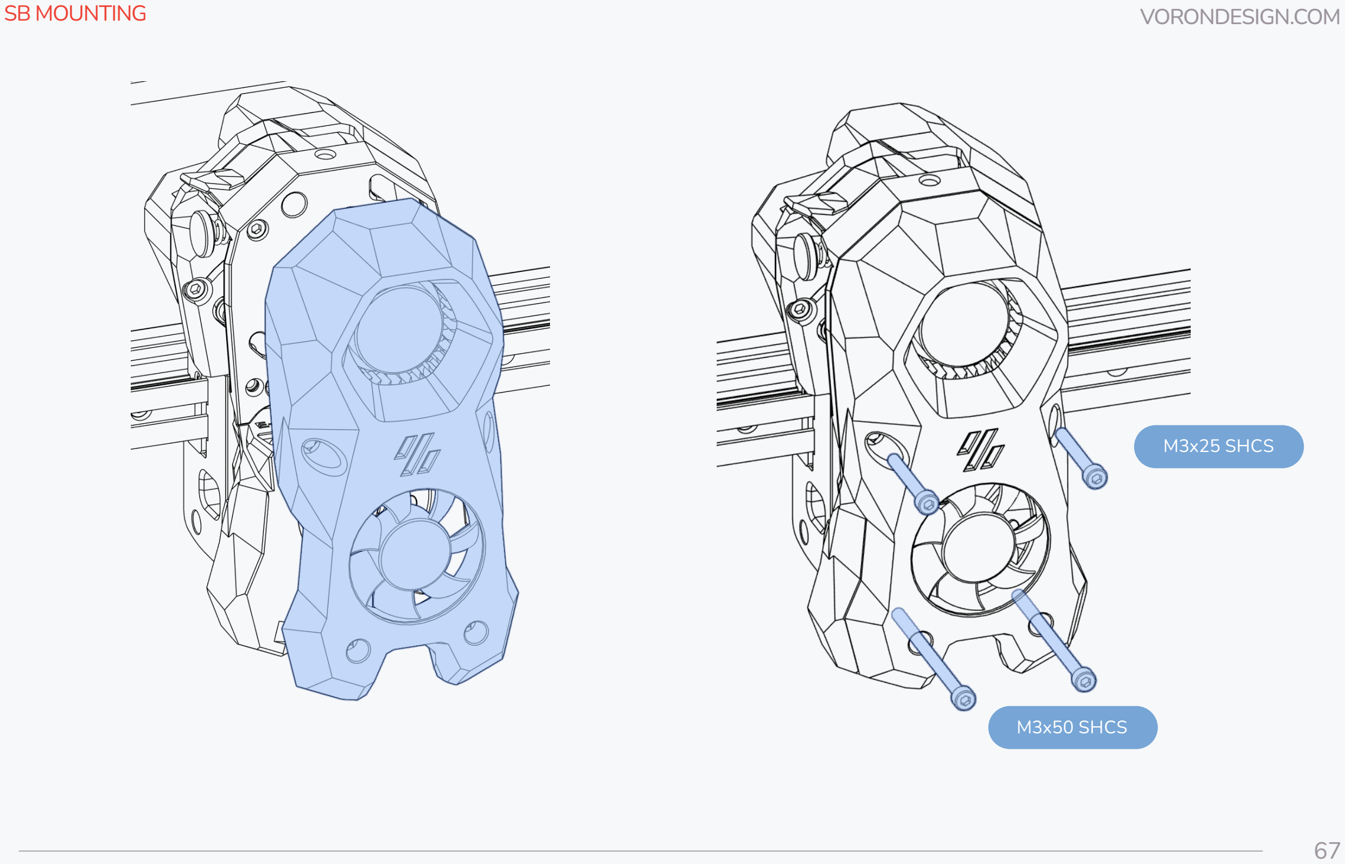
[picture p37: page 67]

67

M3x50 SHCS

M3x25 SHCS

68

ADXL345 MOUNT | VORONDESIGN.COM

69

## VORONDESIGN.COM

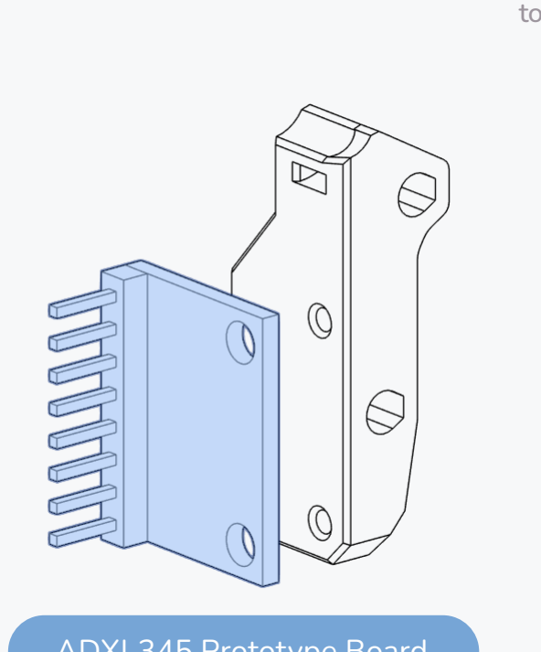
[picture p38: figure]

ADXL345 Prototype Board

ISOLATION SPACERS
Most ADXL345 prototype boards have circuit tracks close to the mounting holes. Make sure to install spacers to prevent damage to the board. We included printable spacers in the release.

## ADXL345 MOUNT

ADXL MOUNT AND INPUT SHAPER CALIBRATION
The ADXL is intended to be mounted only when doing vibration testing/input shaper calibration and should not be left on the tool head during normal printing.

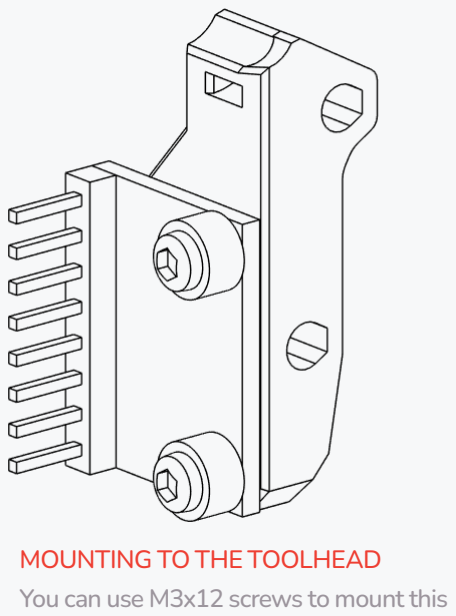
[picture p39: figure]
MOUNTING TO THE TOOLHEAD You can use M3x12 screws to mount this

assembly to your tooolhead.

70

## VORONDESIGN.COM

ASSEMBLY COMPLETED! ... NEXT STEP: SETUP & CALIBRATION
This manual is designed to be a reference manual for the build process of a Voron StealthBurner toolhead. Additional details about the build and background on advanced topics can be found on our documentation page linked below.

The software setup and other initial setup steps with your new printer can also be found on our documentation page. We recommend starting here. (https://docs.vorondesign.com/build/software/)

## https://github.com/VoronDesign/Voron-Stealthburner

## NEXT STEPS

## https://docs.vorondesign.com

# DOCS (https://docs.vorondesign.com)

71

## VORONDESIGN.COM

HOW TO GET HELP
If you need assistance with your build, we’re here to help. Head on over to our Discord group and post your questions. This is our primary medium to help VORON Users and we have a great community that can help you out if you get stuck. Alternatively, you can use our subreddit.

## https://discord.gg/voron

REPORTING ISSUES
Should you find an issue in this document or have a suggestion for an improvement please consider opening an issue on GitHub (https://github.com/VoronDesign/Voron-Stealthburner/issues).

When raising an issue please include the relevant page numbers and a brief description; annotated screenshots are also very welcome.

We periodically update the manual based on the feedback we get.

## https://www.reddit.com/r/VORONDesign

72

## WWW.VORONDESIGN.COM

Github
github.com/vorondesign

Website
vorondesign.com

Discord
discord.gg/voron

# VORON

Docs
docs.vorondesign.com

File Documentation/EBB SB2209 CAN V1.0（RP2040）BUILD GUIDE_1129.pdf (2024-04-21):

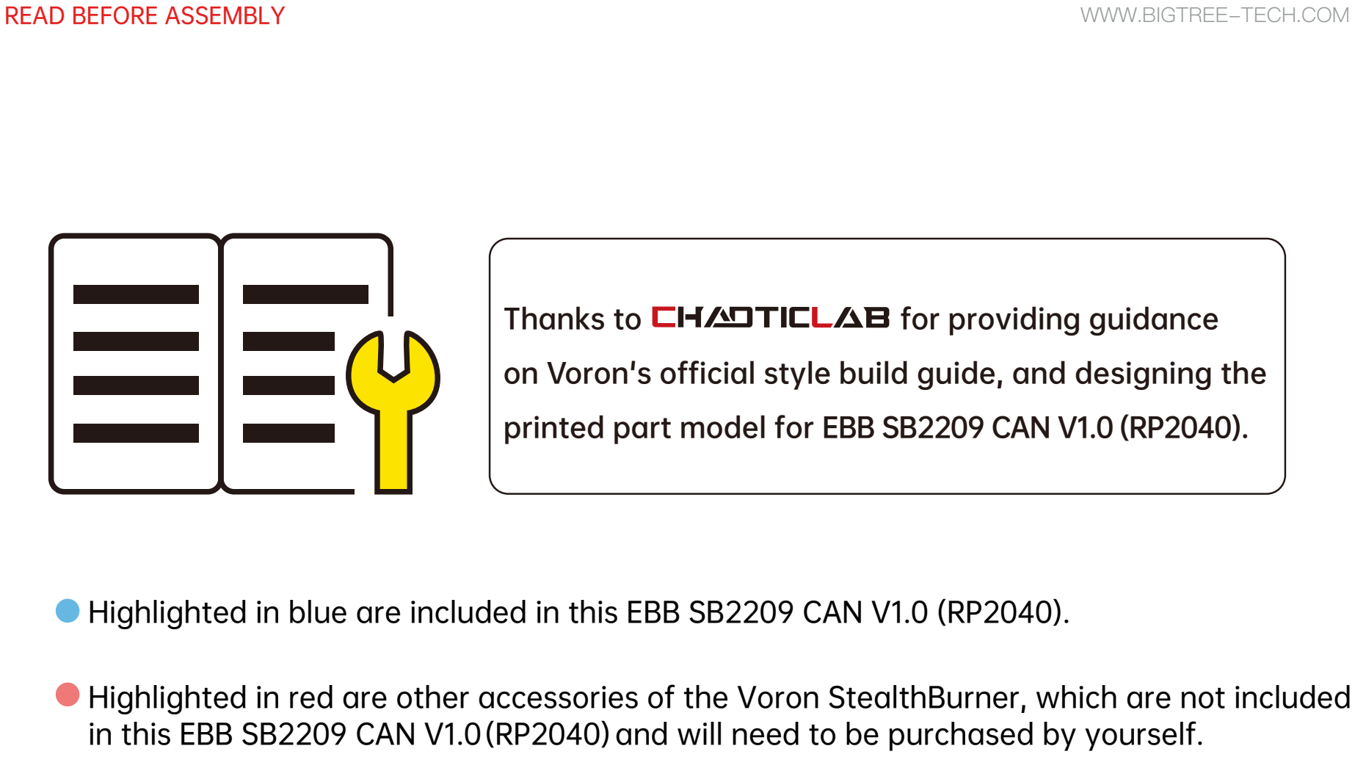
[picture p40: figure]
READ BEFORE ASSEMBLY; Thanks to; for providing guidance; WWW.BIGTREE-TECH.COM

Highlighted in blue are included in this EBB SB2209 CAN V1.0 (RP2040).

Highlighted in red are other accessories of the Voron StealthBurner, which are not included in this EBB SB2209 CAN V1.0(RP2040)and will need to be purchased by yourself.

### on Voron's official style build guide, and designing the

printed part model for EBB SB2209 CAN V1.0 (RP2040).

TABLE OF CONTENTS

TABLE OF CONTENTS

### Packing List

### Table of Contents

Klipper

Compile Firmware

Firmware Update (via DFU)

Firmware Update (via Canboot)

StealthBurner
EBB SB0000 CAN v1.0 Overview Turbine Fan
Axial Fan
PWM Fan
LED

ClockWork2
EBB SB2209 CAN V1.0(RP2040)Overview Install EBB SB2209 CAN V1.0 (RP2040）

Extruder Motor

CAN BUS 120R Termination Resistor

Thermistor
PT100/1000
Heater Cartridge
X-Carriage
Proximity Switch
X Axis Limit Switch
Voron Tap
BLTouch

StealthBurner Final Assembly
CW2 Cable Bridge
Fix CAN / USB-C Cable
StealthBurner to Mainboard Wiring

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
Flashing CanBoot | 25

CAN bus Configure
Klipper Configure | 38

Crimp Terminal
2.0 mm pitch
3.0 mm pitch
2.54 mm pitch
2.0 mm Pitch Connector Housing
3Way
4Way
5Way
2.54mm Pitch Connector Housing
1Way
3.0 mm Pitch Connector Housing
2Way
Jumper

BIGTREETECH EBB SB2209 CAN V1.0 (RP2040）

BIGTREETECH EBB SB0000 CAN V1.0

Insulated Wire Ferrule

CAN bus Cable

M3 x 10 Button Head Cap Screw (BHCS)

## RGB (5V)

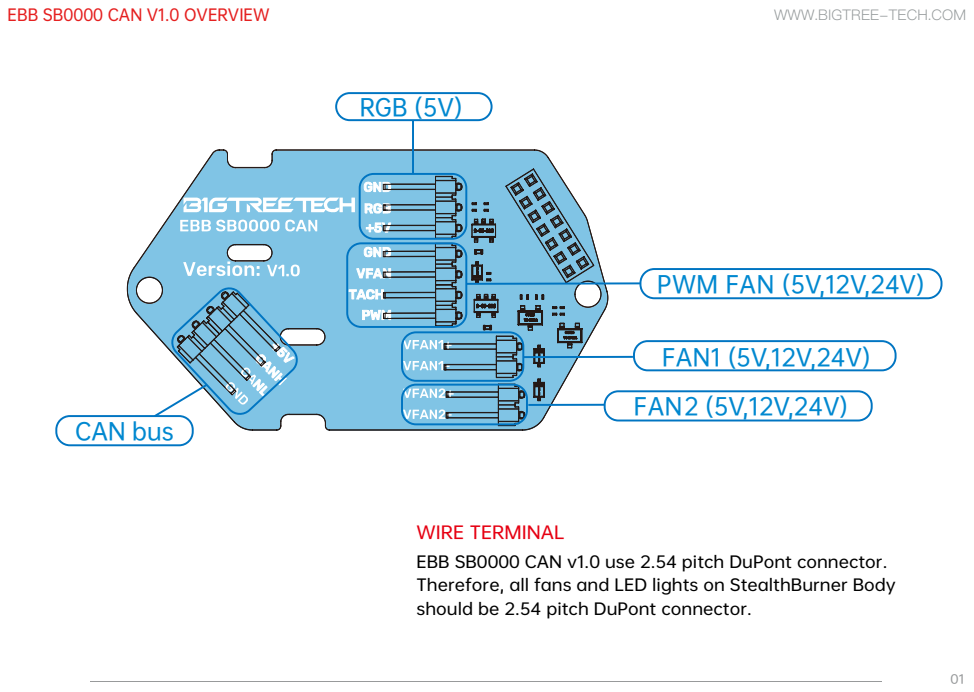
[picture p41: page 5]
PWM FAN (5V,12V,24V); FAN1 (5V,12V,24V) FAN2 (5V,12V,24V); CAN bus

EBB SB0000 CAN V1.0 OVERVIEW

WIRE TERMINAL
EBB SB0000 CAN v1.0 use 2.54 pitch DuPont connector.
Therefore, all fans and LED lights on StealthBurner Body
should be 2.54 pitch DuPont connector.

EBB SB0000 CAN V1.0 OVERVIEW

TIPS
Install 5015 turbine fan, 4010 axial fan, and LED lamp before
installing EBB SB0000 CAN v1.0.

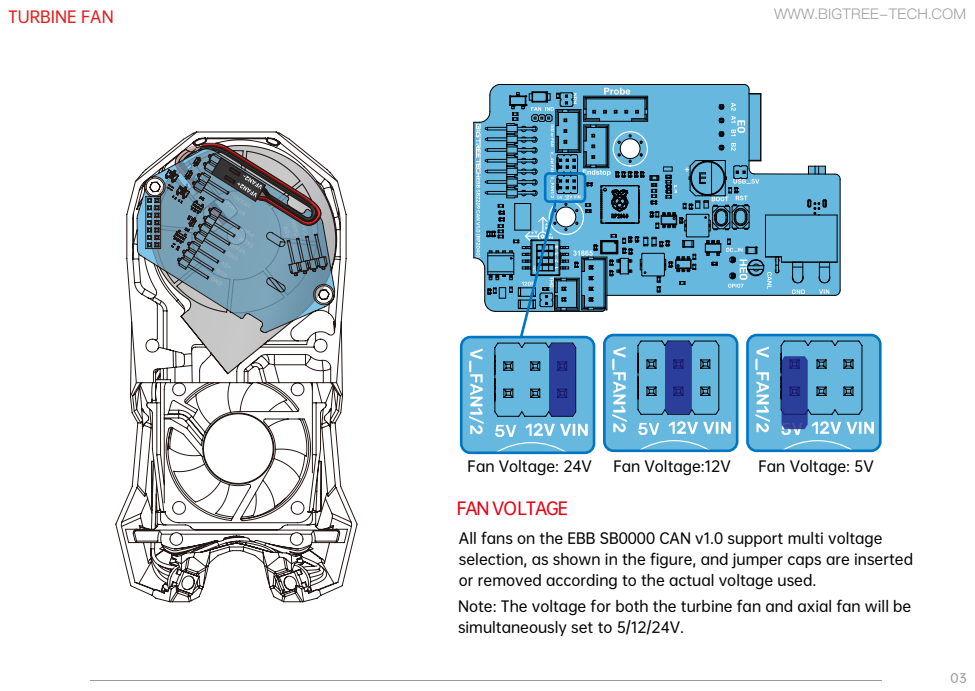
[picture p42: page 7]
TURBINE FAN; Fan Voltage: 24V Fan Voltage:12V; Fan Voltage: 5V

FAN VOLTAGE
All fans on the EBB SB0000 CAN v1.0 support multi voltage
selection, as shown in the figure, and jumper caps are inserted
or removed according to the actual voltage used.
Note: The voltage for both the turbine fan and axial fan will be
simultaneously set to 5/12/24V.

FAN VOLTAGE
All fans on the EBB SB0000 CAN v1.0 support multi voltage
selection, as shown in the figure, and jumper caps are inserted
or removed according to the actual voltage used.
Note: The voltage for both the turbine fan and axial fan will be
simultaneously set to 5/12/24V.

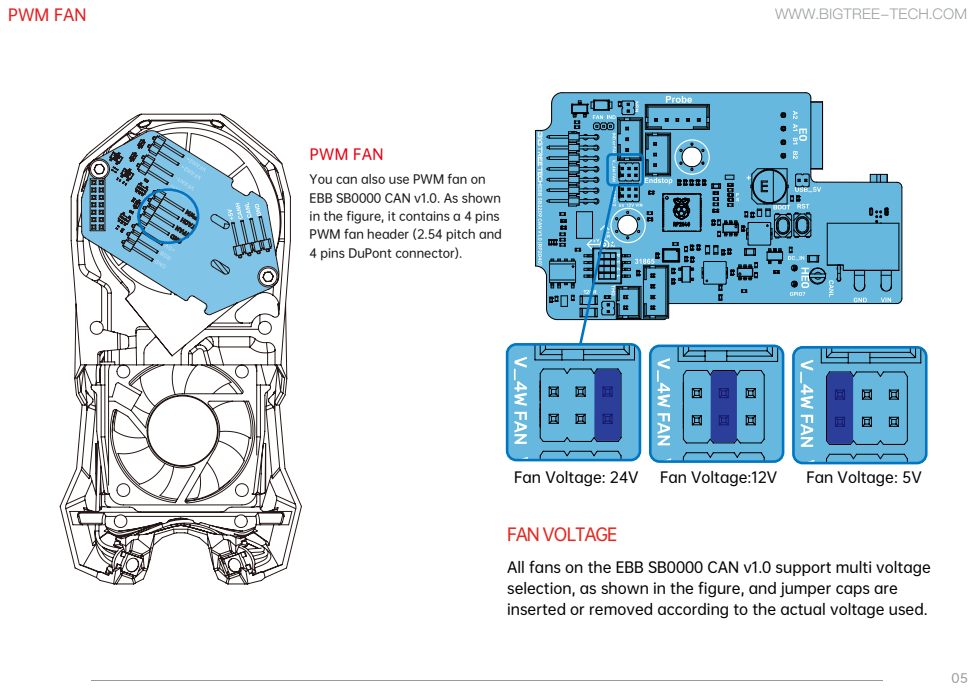
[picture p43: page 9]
PWM FAN; WWW.BIGTREE-TECH.COM; Fan Voltage: 24V Fan Voltage:12V; Fan Voltage: 5V

PWM FAN
You can also use PWM fan on
EBB SB0000 CAN v1.0. As shown
in the figure, it contains a 4 pins
PWM fan header (2.54 pitch and
4 pins DuPont connector).

FAN VOLTAGE
All fans on the EBB SB0000 CAN v1.0 support multi voltage
selection, as shown in the figure, and jumper caps are
inserted or removed according to the actual voltage used.

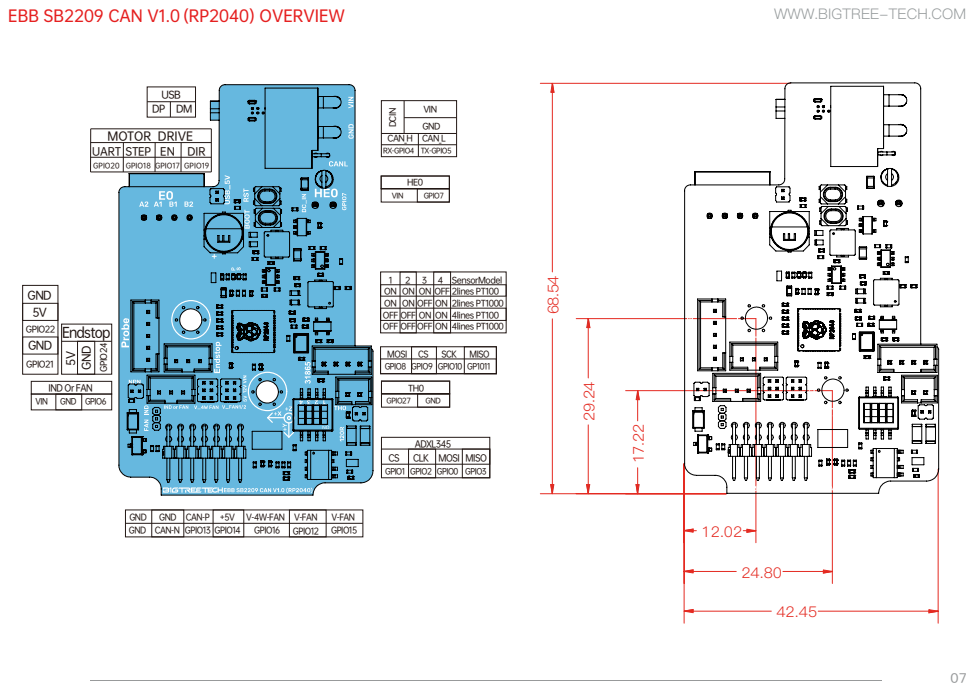
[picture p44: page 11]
EBB SB2209 CAN V1.0 (RP2040) OVERVIEW; WWW.BIGTREE-TECH.COM; ADXL345 CS CLK MOSI MISO; VIN; DCIN; GND; CAN_H; CAN_L; RX-GPIO4; TX-GPIO5; USB; MOTOR DRIVE; GPIO1 GPIO2 GPIO0 GPIO3; IND Or FAN VIN GND GPIO6; GPIO7; 5V GPIO22; GPIO21; Endstop 5V GN GPIO²⁴; GPIO27

UART STEP | | EN | DIR
GPIO20 | GPIO18 | GPIO17 | GPIO19

3 4 SensorModel
ON ON ON OFF 2lines PT100
ON ON OFF ON 2lines PT1000
OFF OFF ON ON 4lines PT100
OFF OFFOFF ON 4lines PT1000

MOSI | CS | SCK | MISO
GPIO8 | GPIO9 | GPIO10 | GP1011

GND | GND | CAN-P | +5V | V-4W-FAN | V-FAN | V-FAN
GND | CAN-N | GPIO13 GPIO14 | | GPIO16 | GPIO12 | GPIO15

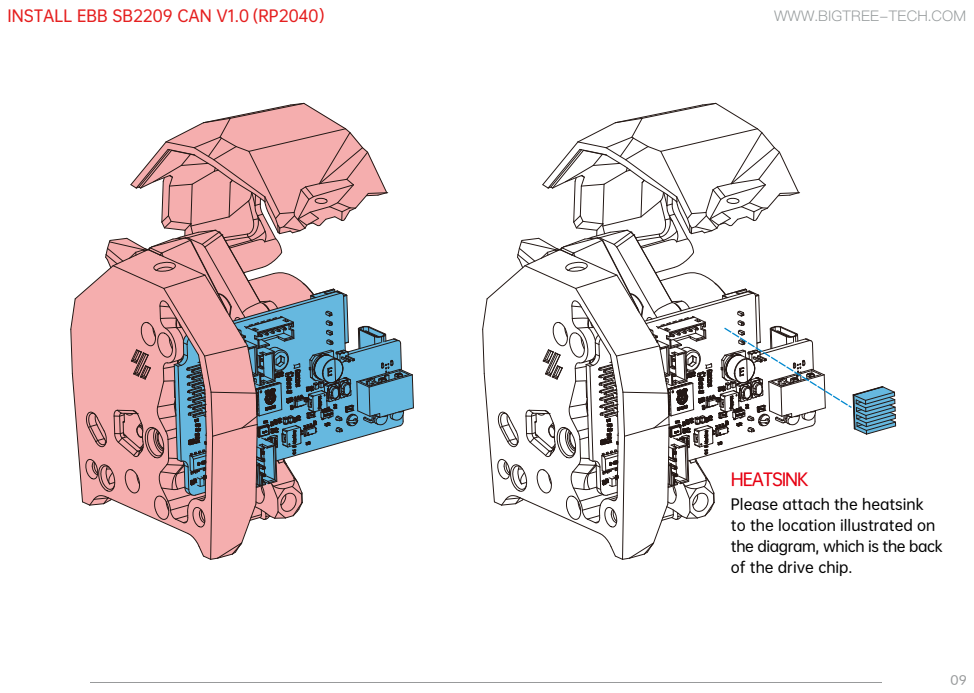
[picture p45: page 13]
INSTALL EBB SB2209 CAN V1.0 (RP2040）; WWW.BIGTREE-TECH.COM

HEATSINK
Please attach the heatsink
to the location illustrated on
the diagram, which is the back
of the drive chip.

CAN BUS 120R TERMINATION RESISTOR

When the EBB SB2209 CAN V1.0 (RP2040) device uses CAN bus communication, if it is the final device in
the CAN bus chain, you must plug a jumper at the 120R position.

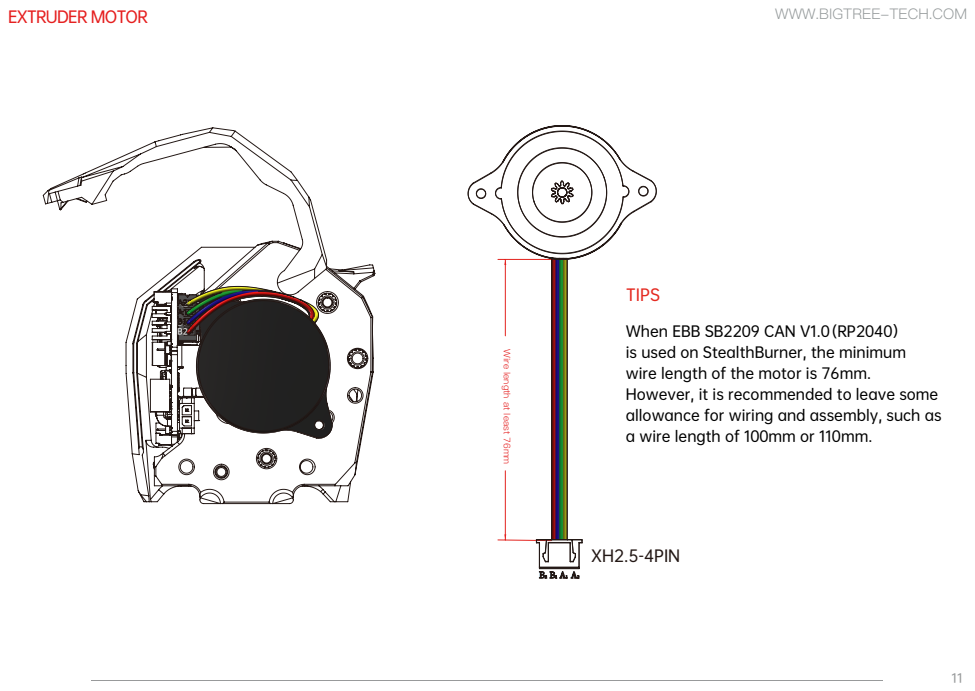
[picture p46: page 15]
EXTRUDER MOTOR; XH2.5-4PIN

TIPS
When EBB SB2209 CAN V1.0(RP2040）
is used on StealthBurner, the minimum
wire length of the motor is 76mm.
However, it is recommended to leave some
allowance for wiring and assembly, such as
a wire length of 100mm or 110mm.

Wire length at least 76mm

PH2.0-2PINWire length shall be at least 103mm

TIPS
When EBB SB2209 CAN V1.0 (RP2040) is
used on StealthBurner, the minimum wire
length of the thermistor is 103mm. However,
it is recommended to leave some allowance
for wiring and assembly, such as a wire length

TIPS
EBB SB2209 CAN V1.0(RP2040) is compatible with 2-wire and
4-wire PT100 or PT1000, but not 3-wire PT100 or PT1000.
As shown in the figure, wire and adjust the dial switch
according to the actual model. And the terminals are PH2.0.

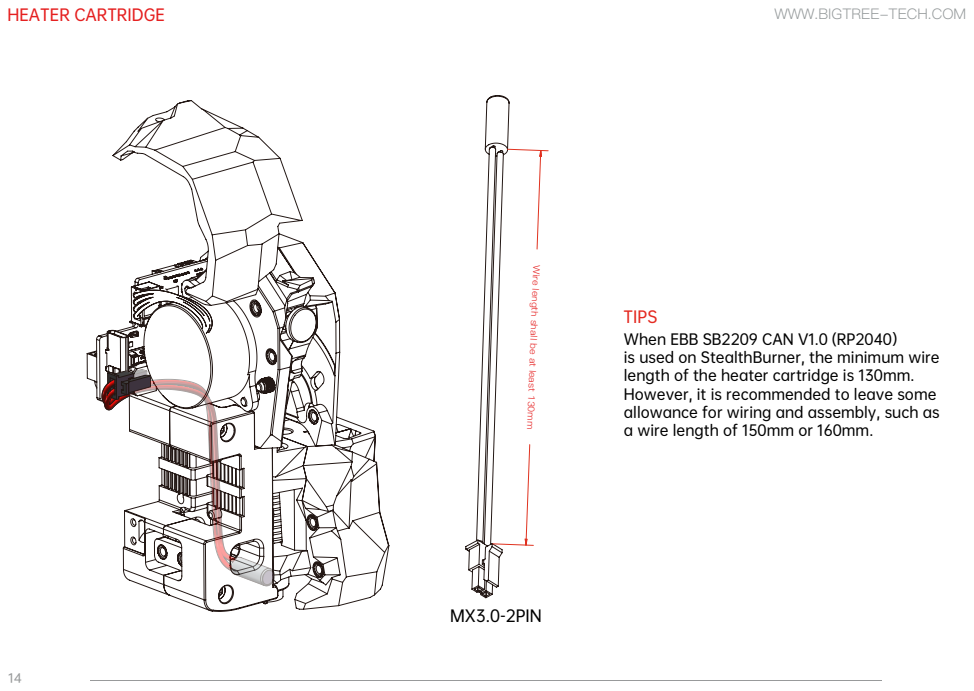
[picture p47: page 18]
HEATER CARTRIDGE

MX3.0-2PINWire length shall be at least 130mm

TIPS
When EBB SB2209 CAN V1.0 (RP2040）
is used on StealthBurner, the minimum wire
length of the heater cartridge is 130mm.
However, it is recommended to leave some
allowance for wiring and assembly, such as
a wire length of 150mm or 160mm.

PROXIMITY SWITCH | WWW.BIGTREE-TECH.COM

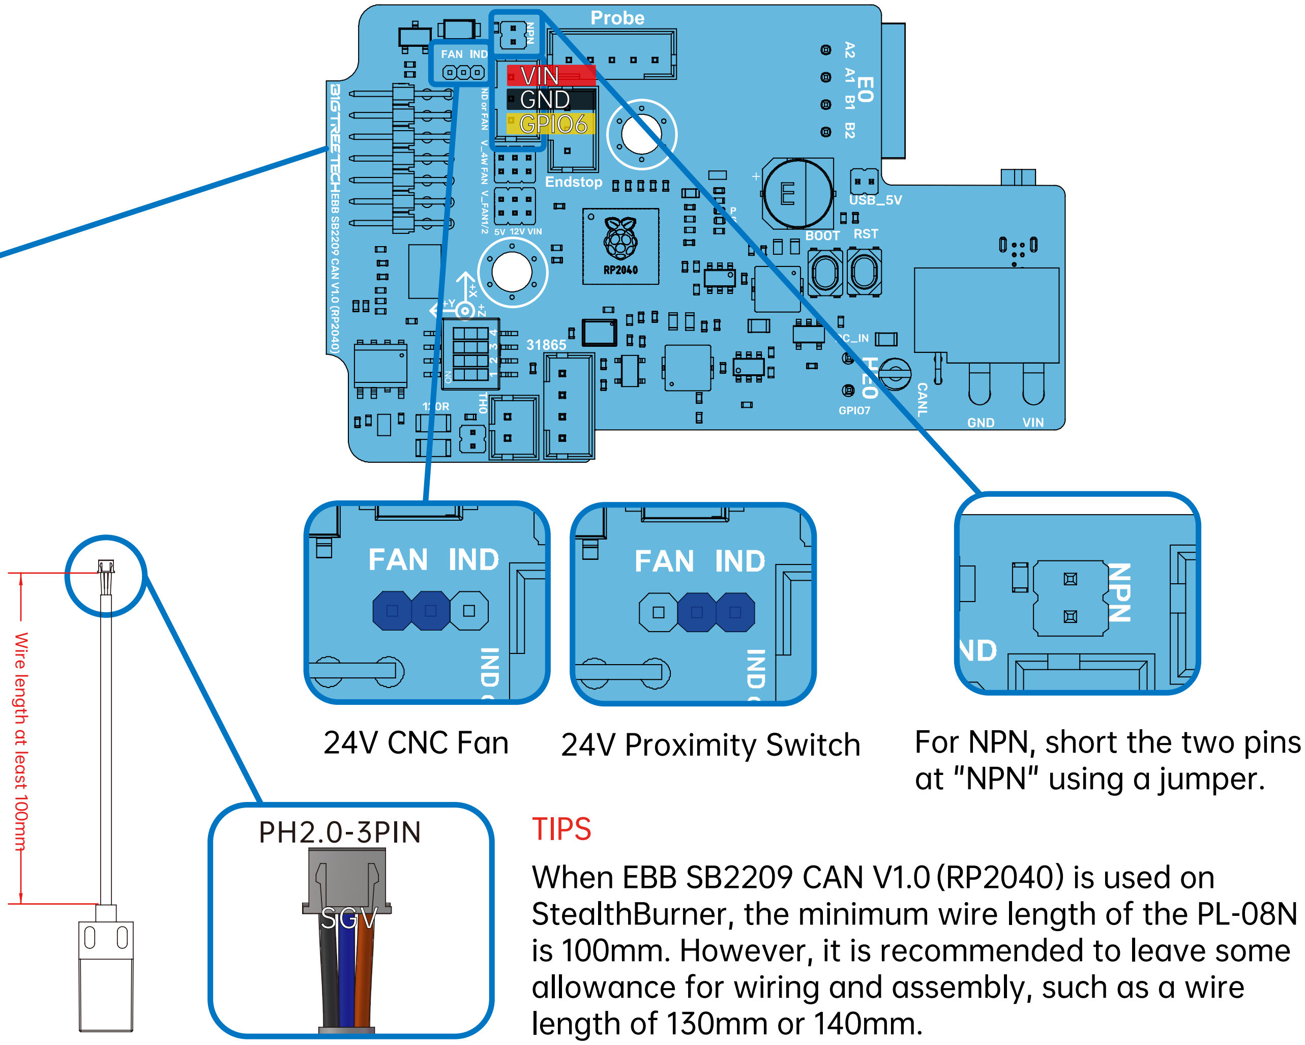
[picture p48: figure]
TIPS; length of 130mm or 140mm.; For NPN, short the two pins at "NPN" using a jumper.; 24V CNC Fan; 24V Proximity Switch; Wire length at least 100mm; VIN GND GPIO6; SGV; PH2.0-3PIN

When EBB SB2209 CAN V1.0 (RP2040）is used on StealthBurner, the minimum wire length of the PL-08N is 100mm. However, it is recommended to leave some allowance for wiring and assembly, such as a wire

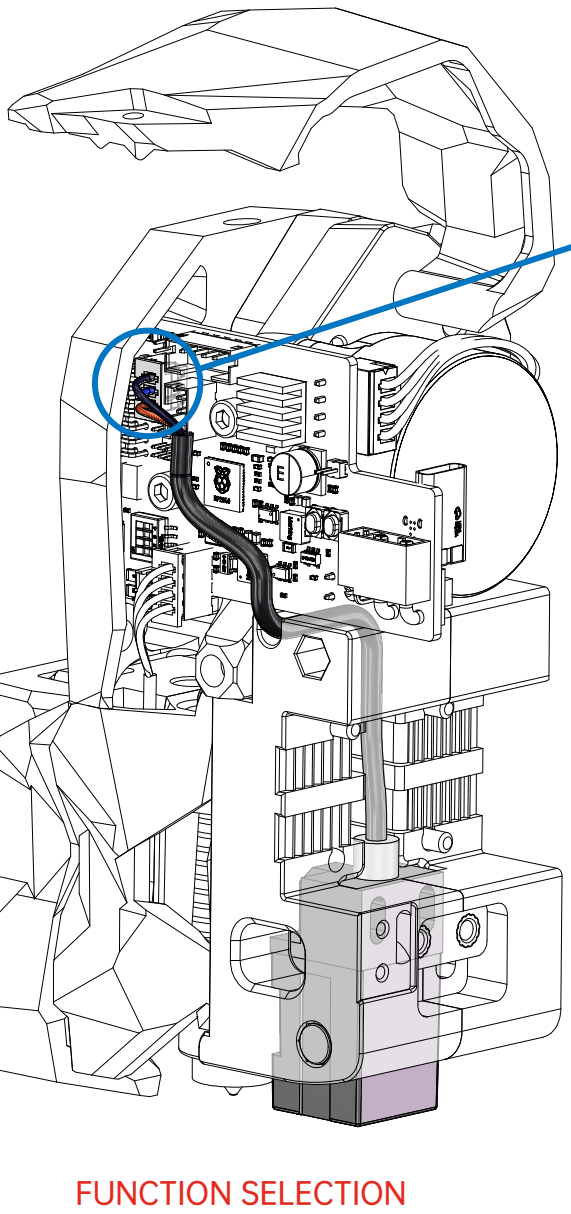
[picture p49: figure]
FUNCTION SELECTION

Supports both NPN and PNP types. For NPN, short the two pins at "NPN" using a jumper; for PNP, remove the jumper.
Note: This interface can also be used for 24V CNC fans. By shorting the left two-pin connector with a jumper (FAN), it can be used for a 24V CNC fan. By shorting the right two-pin connector with a jumper (IND), it can be used for a 24V proximity switch.

to X-Axis Limit switch

END-STOP SWITCHES FOR X
End-stops are wired in a "Normally Closed"
configuration. On microswitches those are
the 2 outer terminals indicated by C and NC.

TIPS
When EBB SB2209 CAN V1.0(RP2040）is used on StealthBurner,
the minimum wire length of the X Axis Limit Switch is 145mm.
However, it is recommended to leave some allowance for wiring
and assembly, such as a wire length of 165mm or 175mm.

Wire length at least 145mm

# PH2.0-5PIN GPIO22

## Voron Tap

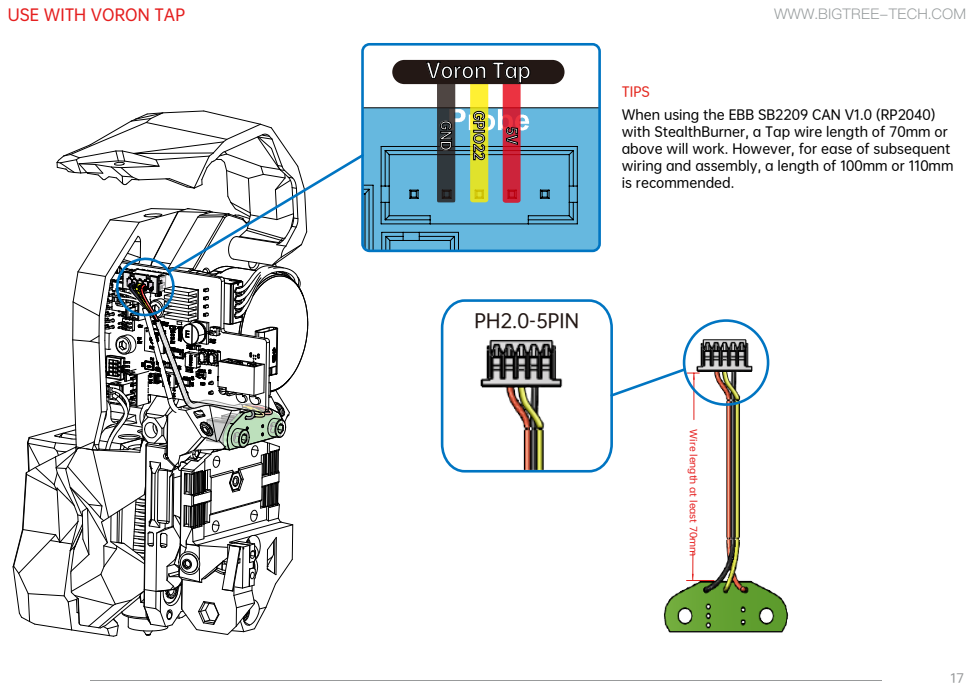
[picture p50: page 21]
USE WITH VORON TAP; WWW.BIGTREE-TECH.COM; GND

TIPS
When using the EBB SB2209 CAN V1.0 (RP2040)
with StealthBurner, a Tap wire length of 70mm or
above will work. However, for ease of subsequent
wiring and assembly, a length of 100mm or 110mm
is recommended. Wire length at least 70mm

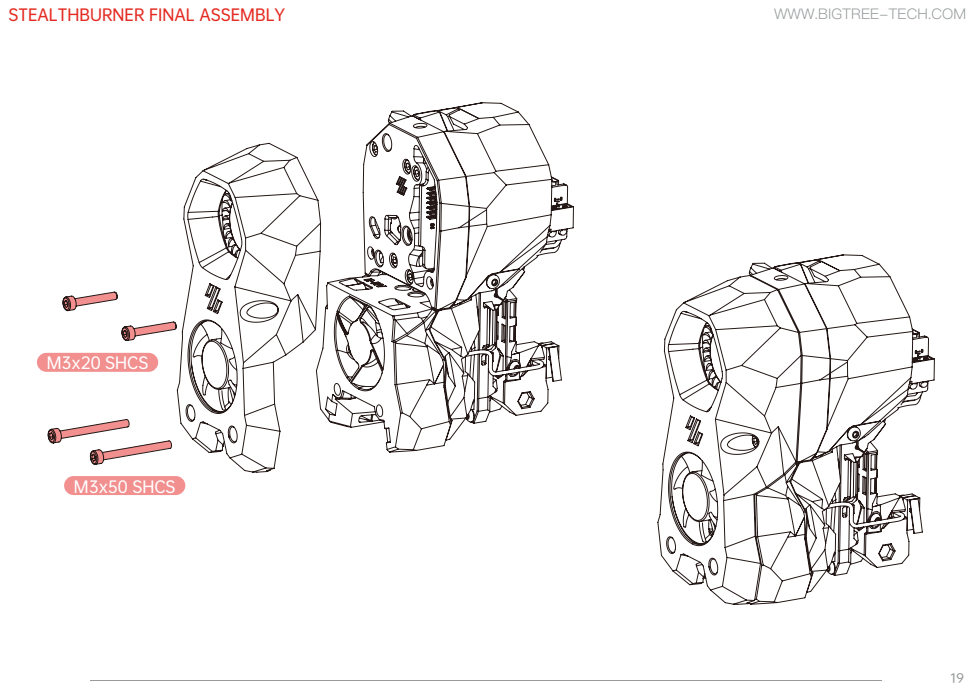
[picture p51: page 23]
STEALTHBURNER FINAL ASSEMBLY; WWW.BIGTREE-TECH.COM; M3x20 SHCS; M3x50 SHCS

TIPS
The CW2 cable bridge is different from the official version, it is a custom printed part that can be downloaded
directly from our GitHub repository, in EBB\EBB SB2240_2209 CAN\Custom Printed Parts.

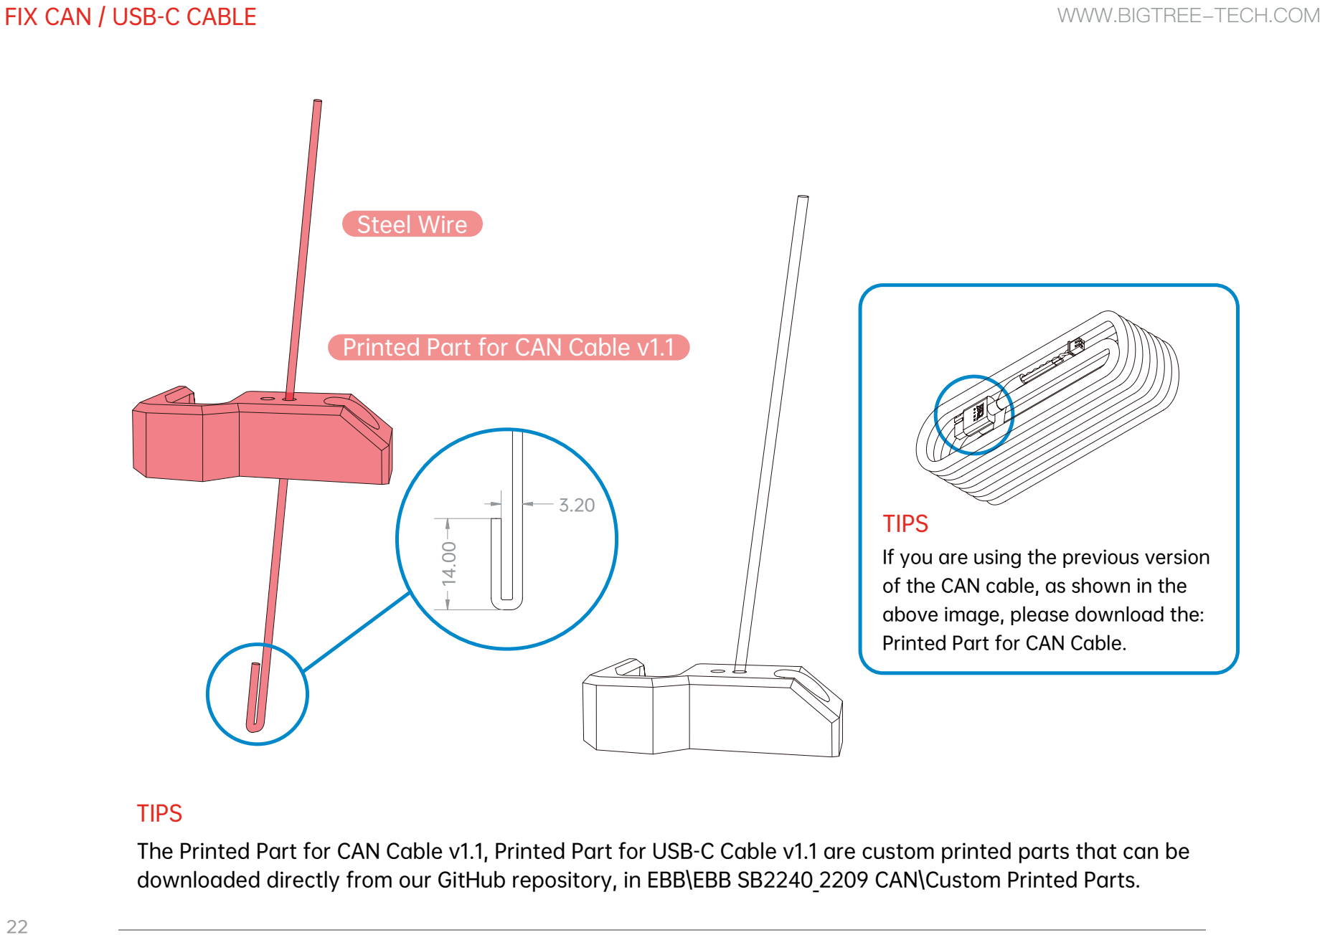
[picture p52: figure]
FIX CAN / USB-C CABLE; WWW.BIGTREE-TECH.COM; Steel Wire; Printed Part for CAN Cable v1.1; TIPS; TIPS If you are using the previous version of the CAN cable, as shown in the above image, please download the: Printed Part for CAN Cable.

The Printed Part for CAN Cable v1.1, Printed Part for USB-C Cable v1.1 are custom printed parts that can be downloaded directly from our GitHub repository, in EBB\EBB SB2240_2209 CAN\Custom Printed Parts.

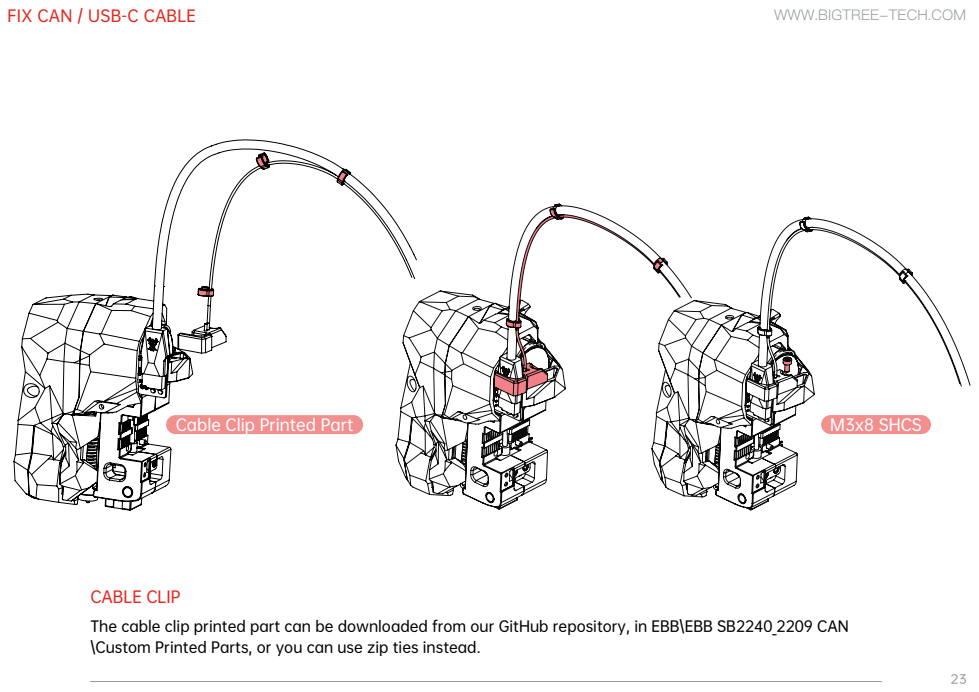
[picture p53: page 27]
Cable Clip Printed Part; M3x8 SHCS

FIX CAN / USB-C CABLE

CABLE CLIP
The cable clip printed part can be downloaded from our GitHub repository, in EBB\EBB SB2240_2209 CAN
\Custom Printed Parts, or you can use zip ties instead.

STEALTHBURNER TO MAINBOARD WIRING

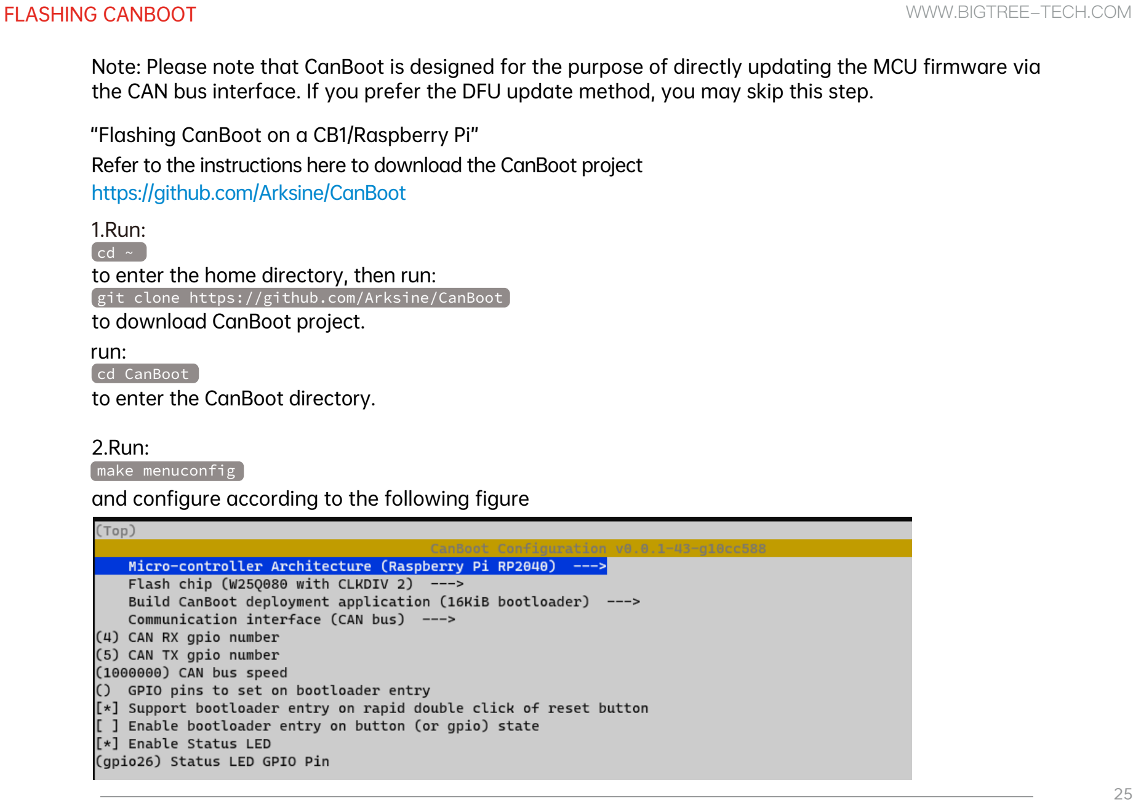
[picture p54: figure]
FLASHING CANBOOT; https://github.com/Arksine/CanBoot 1.Run: cd ~ to enter the home directory, then run: git clone https://github.com/Arksine/CanBoot to download CanBoot project. run: cd CanBoot to enter the CanBoot directory.; 2.Run: make menuconfig

Refer to the instructions here to download the CanBoot project

and configure according to the following figure

“Flashing CanBoot on a CB1/Raspberry Pi”

Note: Please note that CanBoot is designed for the purpose of directly updating the MCU firmware via the CAN bus interface. If you prefer the DFU update method, you may skip this step.

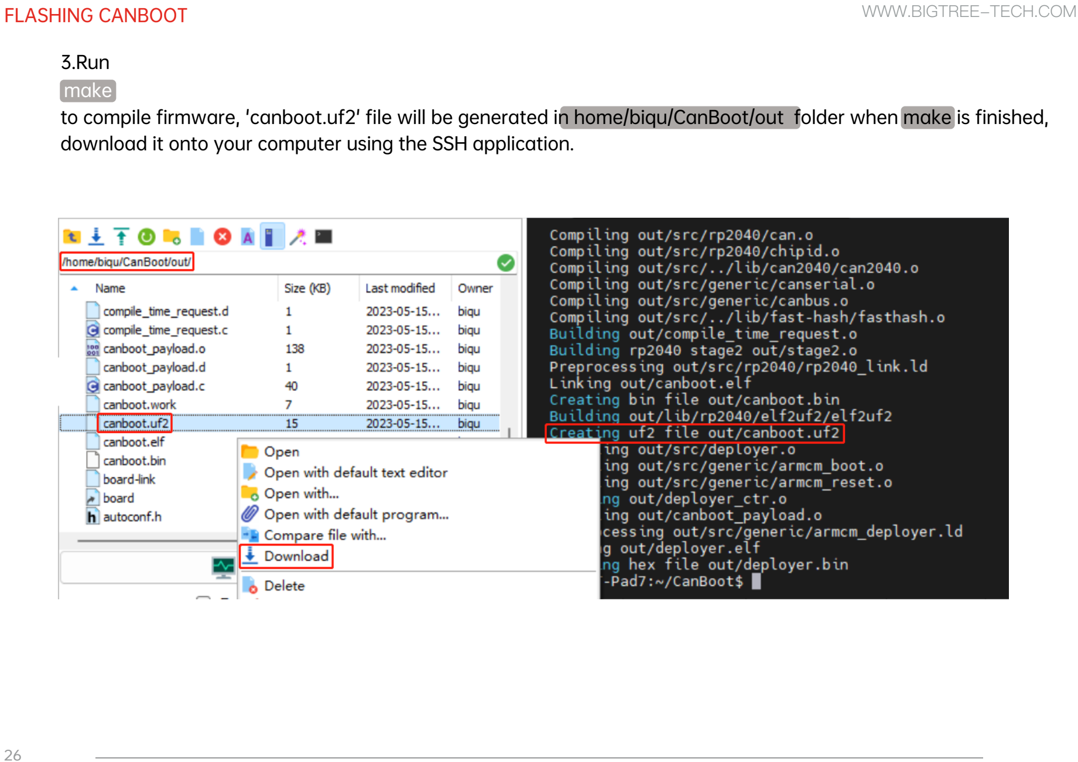
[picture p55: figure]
FLASHING CANBOOT; 3.Run make

to compile firmware, 'canboot.uf2' file will be generated in home/biqu/CanBoot/out folder when make is finished, download it onto your computer using the SSH application.

USB_5V; FLASHING CANBOOT; WWW.BIGTREE-TECH.COM

4.1 Please use a Type-C cable to connect the EBB SB2209 CAN V1.0(RP2040)
to the Raspberry Pi/CB1, and ensure that the USB_5V jumper is connected, in order
to supply power to the EBB SB2209 CAN V1.0(RP2040) via Type-C.

4.2. Press and hold the Boot button, and then click
the Reset button to enter the DFU mode.

4.3. Enter in the SSH terminal command line
4.4. Please enter the following command to flash CanBoot:

lsusb

Query DFU device ID

pi@fluiddpi:~ $ lsusb
Bus | 001 | Device | 005: | ID | 2e8a:0003 | Raspberry Pi RP2 Boot
Bus | 001 | Device | 004: | ID | 1d50:6061 | OpenMoko, Inc. Geschwister Schneider CAN adapter
Bus | 001 | Device | 003: | ID | 0424:0c00 | Microchip Technology, Inc. | ( formerly SMSC ) | SMC9512/9514 | Fast | Ethernet | Adapter
Bus | 001 | Device | 002: | ID | 0424:9514 | Microchip Technology, Inc. | ( formerly SMSC ) | SMC9514 Hub
Bus | 001 | Device | 001: | ID | 1d6b:0002 | Linux Foundation 2.0 root hub
pi@fluiddpi:~ $
4.5. After flashing is complete, remove the USB_5V jumper and the Type-C cable.

where "2e8a:0003" should be replaced with the actual device ID obtained in step 4.3.

FLASHING CANBOOT | WWW.BIGTREE-TECH.COM

make flash FLASH_DEVICE=2e8a:0003

COMPILE FIRMWARE

1.)
cd ~/klipper/
make menuconfig
Compile the firmware with the following configuration (if the options below are not available, please update your Klipper source code to the newest version).

After SSH is successfully connected to Raspberry Pi, run

[*] Enable extra low-level configuration
optionsMicro-controller Architecture
(Raspberry Pi RP2040)--->

Bootloader offset (No bootloader) ---> Flash chip (W25Q080 with CLKDIV 2) --->

Bootloader offset (16KiB bootloader) --->

Communication interface (USB) --->

Communication interface (CAN bus) --->
(4) CAN RX gpio number
(5) CAN TX gpio number
(1000000) CAN bus speed
2.) Press q to exit, and Yes when asked to save
the configuration.
3.) Run make to compile firmware, "klipper. bin" file will be generated in home/pi/klipper/out folder when make is finished, download
it onto your computer using the SSH application.

If you do not use CanBoot

If CanBoot is used

If USB communication on Type-C is used

If CAN-Bus communication is used

2. Run:

then run:

cd ~/CanBoot/scripts

python3 flash_can.py -i can0 -q
to query the canbus ID (connect the CAN cable and power it on in advance), as shown in the figure below, the UUID of the device has been found

1.To use the CAN bus, you need to connect the CAN bus cable and insert a jumper
at the position of the 120R termination resistor.
FIRMWARE UPDATE(VIA CANBOOT) | WWW.BIGTREE-TECH.COM


4. Run:
3. Run:
python3 flash_can.py -i can0 -f ~/klipper/out/klipper.bin -u be69315a613c
The be69315a613c is replaced with the actual UUID. Note: klipper.bin needs to be made in advance, and the application start offset of CanBoot is 16KiB offset, so Klipper's menuconfig Bootloader offset should also be 16KiB bootloader, as shown in the following figure.


python3 flash_can.py -i can0 -q
to query. At this time, the Application changes from CanBoot to Klipper, indicating that Klipper has been running normally
FIRMWARE UPDATE(VIA CANBOOT) | WWW.BIGTREE-TECH.COM

USB_5V

FIRMWARE UPDATE(VIA DFU)

Raspberry Pi or CB1 update via DFU.
1. Please use a Type-C cable to connect the EBB SB2209 CAN V1.0 (RP2040) to the Raspberry Pi/CB1,
and ensure that the USB_5V jumper is connected, in order to supply power to the
EBB SB2209 CAN V1.0 (RP2040) via Type-C.

2. Press and hold the Boot button, and then click
the Reset button to enter the DFU mode.

FIRMWARE UPDATE (VIA DFU)

3.Enter in the SSH terminal command line lsusb
Query DFU device ID

4.Run:

cd klipper

to enter to the klipper directory, then run the following command to write the firmware:

Note: Replace 2e8a:0003 with the actual device ID found in the previous step.

pi@fluiddpi:~ $ lsusb
Bus | 001 | Device | 005: | ID | 2e8a:0003 | Raspberry Pi RP2 Boot
Bus | 001 | Device | 004: | ID | 1d50:6061 | OpenMoko, Inc. Geschwister Schneider CAN adapter
Bus | 001 | Device | 003: | ID | 0424:0c00 | Microchip Technology, Inc. | ( formerly SMSC ) | SMC9512/9514 | Fast | Ethernet | Adapter
Bus | 001 | Device | 002: | ID | 0424:9514 | Microchip Technology, Inc. | ( formerly SMSC ) | SMC9514 Hub
Bus | 001 | Device | 001: | ID | 1d6b:0002 | Linux Foundation 2.0 root hub
pi@fluiddpi:~ $

make flash FLASH_DEVICE=2e8a:0003

FIRMWARE UPDATE (VIA DFU)

6. If USB communication is used, after the first writing, it is not necessary to manually press the Boot and Reset buttons to enter the DFU mode when updating again.
You can directly enter

to write the firmware (Note: replace/dev/serial/by id/xxx with the actual ID found in the previous step).

5. After the firmware is written, run

ls /dev/serial/by-id/

to query the serial ID of the device (this ID can only be found in the USB communication mode, and this step is ignored in CANBus mode).

make flash FLASH_DEVICE=/dev/serial/by-id/usb-Klipper_rp2040_4550357128922FC8-if00

After flashing is complete, remove the USB_5V jumper and the Type-C cable.

CAN BUS CONFIGURE

Used with BIGTREETECH U2C module.

1. Enter the command

sudo nano /etc/network/interfaces.d/can0
in the SSH terminal and execute

allow-hotplug can0
iface can0 can static
bitrate 1000000
up ifconfig $IFACE txqueuelen 1024
Set the CAN-BUS speed to 1M (it must be consistent with the speed set in the firmware (1000000) CAN bus speed), save (Ctrl+S)
and exit (Ctrl+X) after modification, and enter

sudo reboot
to restart Raspberry Pi.
2. Each device on CAN bus will generate a canbus_uuid according to the UID of MCU, to find each
microcontroller device ID, make sure the hardware
is powered on and wired correctly, and then run:

~/klippy-env/bin/python ~/klipper/scripts/canbus_query.py can0

4. If Klipper has been running normally and connected to this device, then canbus_uuid will not be reported, which is normal.
3. If an uninitialized CAN device is detected, the above command will report the device's canbus_uuid.

Found canbus_uuid=0e0d81e4210c

KLIPPER CONFIGURE

1. Enter Raspberry Pi IP address into your browser, and find the reference config for the motherboard in the directory shown below, if there is no such config available, update your Klipper source code to the newest version or download it from GitHub:

https://github.com/bigtreetech/EBB

2. Upload the configuration file of the motherboard to Configuration Files.
KLIPPER CONFIGURE | WWW.BIGTREE-TECH.COM


[include sample-bigtreetech-ebb-sb-canbus-v1.0.cfg]; https://www.klipper3d.org/Overview.html; sample-bigtreetech-ebb-sb-canbus-v1.0.cfg; [mcu EBBCan]; serial /dev/serial/by-id/usb-Klipper_firmware_12345-if00; #canbus_uuid: 0e0d81e4210c; printer.cfg; [include sample-bigtreetech-ebb-canbus-v1.0.cfg]; KLIPPER CONFIGURE; WWW.BIGTREE-TECH.COM

3. Add the configuration of this motherboard in the "printer. cfg" file:
4. Enter the correct ID (USB serial or canbus).
5. Configure the module's specific functions according to


Websit

e
www.bigtree-tech.com

Disco

r

d
www.discord.gg/5jdwbYYZuv

GitHub
www.github.com/bigtreetech

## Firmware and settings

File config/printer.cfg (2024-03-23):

[include moonraker_obico_macros.cfg]

########################################################################################################################### CONFIG INCLUDES

[include KAMP_Settings.cfg]
[include start.cfg]
[include filament.cfg]
[include macros.cfg]
[include KNOMI.cfg]
[include EBBCan.cfg]
[include stealthburner_leds.cfg]
[include temperature_led.cfg]
[include sensorless.cfg]
#[include adxl.cfg]


########################################################################################################################### MCU

[mcu]
serial:/dev/serial/by-id/usb-Klipper_stm32h743xx_3D003E001251303232383230-if00
restart_method: command

########################################################################################################################### SPEED/ACCEL SETTINGS

[printer]
kinematics: cartesian
max_velocity: 300
max_accel: 3000
#max_accel_to_decel: 500
max_z_velocity: 15
max_z_accel: 100
#square_corner_velocity:2

########################################################################################################################### POWER-ON GCODE

[delayed_gcode set_temeperature_leds]
initial_duration: 1
gcode:
     STATUS_READY

########################################################################################################################### MAINSAIL MISC

[pause_resume]

[save_variables]
filename: ~/printer_data/variables.cfg # UPDATE THIS FOR YOUR PATH!!!

[virtual_sdcard]
path: ~/printer_data/gcodes
on_error_gcode: CANCEL_PRINT

[exclude_object]

[display_status]

[gcode_arcs]
resolution: 0.1

[idle_timeout]
timeout: 3600 # Idle time (in seconds)

########################################################################################################################### HEATER CHECKS

[verify_heater extruder]
max_error: 60
check_gain_time:20
hysteresis: 5
heating_gain: 2

[verify_heater heater_bed]
max_error: 240
check_gain_time:180
hysteresis: 5
heating_gain: 1 

########################################################################################################################### STEPPER X

[stepper_x]
step_pin: PD4
dir_pin: !PD3
enable_pin: !PD6
microsteps: 16
rotation_distance: 72
endstop_pin: tmc2209_stepper_x:virtual_endstop
#endstop_pin: ^PE15
position_endstop: -6
position_min: -6
position_max: 505
homing_speed: 80
homing_retract_dist: 2
step_pulse_duration:0.000002

[tmc2209 stepper_x]
uart_pin: PD5
diag_pin: ^PC1 # use the same pin that was previously the endstop_pin!
driver_SGTHRS: 108 # 255 is most sensitive value, 0 is least sensitive. Calibrate this yourself
run_current: 1
#uart_address: 3
#stealthchop_threshold: 999999
#driver_TBL: 2
#driver_TOFF: 2
#driver_HEND: 1
#driver_HSTRT: 4
#driver_PWM_LIM: 8 
#driver_PWM_GRAD: 8
#driver_PWM_FREQ: 1
#driver_PWM_REG: 4

########################################################################################################################### STEPPER Y

[stepper_y]
step_pin: PA15
dir_pin: PA8
enable_pin: !PD1
microsteps: 16
rotation_distance: 72
#endstop_pin: ^PC3
endstop_pin: tmc2209_stepper_y:virtual_endstop 
position_endstop: -10
position_min: -10
position_max: 500
homing_speed: 50
homing_retract_dist: 0
step_pulse_duration:0.000002

[tmc2209 stepper_y]
uart_pin: PD0
diag_pin: ^PC3 # use the same pin that was previously the endstop_pin!
driver_SGTHRS: 107 # 255 is most sensitive value, 0 is least sensitive. Calibrate this yourself!
run_current: 1
#uart_address: 3
#stealthchop_threshold: 999999

[stepper_y1]
step_pin:PD15
dir_pin:!PD14
enable_pin:!PC7
microsteps:16
rotation_distance:72
#endstop_pin: ^PC3
endstop_pin: tmc2209_stepper_y:virtual_endstop

[tmc2209 stepper_y1]
uart_pin:PC6
#diag_pin: ^PE13 # use the same pin that was previously the endstop_pin!
#driver_SGTHRS: 255 # 255 is most sensitive value, 0 is least sensitive
run_current:1 
#uart_address:3
#stealthchop_threshold: 999999

########################################################################################################################### STEPPER Z

[stepper_z]
step_pin: PE2
dir_pin: PE3
enable_pin: !PE0
microsteps: 16
rotation_distance: 4
endstop_pin:probe:z_virtual_endstop
position_max: 505
position_min: -3
homing_speed: 20

[tmc2209 stepper_z]
uart_pin:PE1
run_current:0.6
#uart_address:3
stealthchop_threshold: 999999

[stepper_z1]
step_pin: PD11
dir_pin: PD10
enable_pin: !PD13
microsteps: 16
rotation_distance: 4
endstop_pin:probe:z_virtual_endstop

[tmc2209 stepper_z1]
uart_pin:PD12
run_current:0.6
#uart_address:3
stealthchop_threshold: 999999

########################################################################################################################### BED HEATER

[heater_bed]
heater_pin: PD7
sensor_type: EPCOS 100K B57560G104F
sensor_pin: PA1
#control: pid
#pid_Kp: 75.227
#pid_Ki: 0.807
#pid_Kd: 1748.382
min_temp: 0
max_temp: 95
pwm_cycle_time: 0.0166

########################################################################################################################### PROBE

[probe]
pin: !EBBCan:gpio22
x_offset: 0
y_offset: 0
#z_offset: 0.5 ## CONFIGURE THIS WITH THE Z CALIBRATE TOOL
speed: 10.0
samples: 3
samples_result: median
sample_retract_dist: 3.0
samples_tolerance: 0.006
samples_tolerance_retries: 10
activate_gcode:
    {% set PROBE_TEMP = 180 %}
    {% set MAX_TEMP = PROBE_TEMP + 5 %}
    {% set ACTUAL_TEMP = printer.extruder.temperature %}
    {% set TARGET_TEMP = printer.extruder.target %}

    {% if TARGET_TEMP > PROBE_TEMP %}
        { action_respond_info('Extruder temperature target of %.1fC is too high, lowering to %.1fC' % (TARGET_TEMP, PROBE_TEMP)) }
        M109 S{ PROBE_TEMP }
    {% else %}
        # Temperature target is already low enough, but nozzle may still be too hot.
        {% if ACTUAL_TEMP > MAX_TEMP %}
            { action_respond_info('Extruder temperature %.1fC is still too high, waiting until below %.1fC' % (ACTUAL_TEMP, MAX_TEMP)) }
            TEMPERATURE_WAIT SENSOR=extruder MAXIMUM={ MAX_TEMP }
        {% endif %}
    {% endif %}

########################################################################################################################### Z HOMING

[safe_z_home]
home_xy_position: 250,250
speed: 90
z_hop: 5                 # Move up 5mm
z_hop_speed: 5

########################################################################################################################### BED MESH

[bed_mesh]
speed:190                
horizontal_move_z:4
mesh_min:26,26   
mesh_max:478,474 
probe_count:10,10    
mesh_pps: 2, 3
algorithm: bicubic
bicubic_tension: 0.2 


########################################################################################################################### Z TILT

[z_tilt]
z_positions: 97, 250
             409, 250
points: 97, 250
        409, 250
speed: 200
horizontal_move_z: 5
retries: 20
retry_tolerance: .001

########################################################################################################################### MAINGOARD FANS

[controller_fan Fan_Board]
pin:PB5
fan_speed: 1.0
idle_timeout: 120
heater: heater_bed, extruder
stepper: stepper_x, stepper_y, stepper_y1, stepper_z, stepper_z1
########################################################################################################################### AUTO GENERATED

#*# <---------------------- SAVE_CONFIG ---------------------->
#*# DO NOT EDIT THIS BLOCK OR BELOW. The contents are auto-generated.
#*#
#*# [probe]
#*# z_offset = -0.930
#*#
#*# [extruder]
#*#
#*# [input_shaper]
#*# shaper_type_x = mzv
#*# shaper_freq_x = 42.0
#*# shaper_type_y = ei
#*# shaper_freq_y = 40.2
#*#
#*# [heater_bed]
#*# control = pid
#*# pid_kp = 75.714
#*# pid_ki = 0.992
#*# pid_kd = 1445.196
#*#
#*# [bed_mesh default]
#*# version = 1
#*# points =
#*# 	-0.789990, -0.724990, -0.761240, -0.771240, -0.759990, -0.728740, -0.719990
#*# 	-0.538740, -0.476240, -0.588740, -0.647490, -0.643740, -0.584990, -0.527490
#*# 	-0.337490, -0.324990, -0.426240, -0.501240, -0.477490, -0.408740, -0.351240
#*# 	-0.116240, -0.128740, -0.222490, -0.316240, -0.283740, -0.206240, -0.138740
#*# 	0.007510, -0.009990, -0.103740, -0.177490, -0.149990, -0.054990, 0.008760
#*# 	0.093760, 0.085010, 0.007510, -0.069990, -0.028740, 0.041260, 0.083760
#*# 	0.122510, 0.118760, 0.045010, -0.016240, 0.011260, 0.057510, 0.061260
#*# 	0.103760, 0.115010, 0.043760, 0.003760, 0.013760, 0.023760, 0.003760
#*# 	0.138760, 0.147510, 0.085010, 0.056260, 0.041260, 0.041260, -0.008740
#*# x_count = 7
#*# y_count = 9
#*# mesh_x_pps = 2
#*# mesh_y_pps = 3
#*# algo = bicubic
#*# tension = 0.2
#*# min_x = 100.94
#*# max_x = 399.02
#*# min_y = 53.87
#*# max_y = 446.11

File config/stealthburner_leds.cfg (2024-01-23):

# Macros for setting the status leds on the Voron StealthBurner toolhead (or for any neopixel-type leds).
#
# You will need to configure a neopixel (or other addressable led, such as dotstar). See
# https://www.klipper3d.org/Config_Reference.html#neopixel for configuration details.


#####################################
#           INSTRUCTIONS            #
#####################################
# How to use all this stuff:
#
#     1.  Copy this .cfg file into your Klipper config directory and then add [include stealthburner_leds.cfg]
#         to the top of your printer.cfg in order to register the LEDs and macros with Klipper.
#     2.  Define your LEDs by editing [neopixel sb_leds] below and entering the data pin from your control board
#         as well as the color order.
#
#           Note: RGB and RGBW are different and must be defined explicitly.  RGB and RGBW are also not able to 
#                 be mix-and-matched in the same chain. A separate data line would be needed for proper functioning.
#
#                 RGBW LEDs will have a visible yellow-ish phosphor section to the chip.  If your LEDs do not have
#                 this yellow portion, you have RGB LEDs.
#
#     3.  Save your config and restart Klipper.
#
#           Note: We set RED and BLUE to 1.0 to make it easier for users and supporters to detect 
#                 misconfigurations or miswiring. The default color format is for Neopixels with a dedicated 
#                 white LED. On startup, all three SB LEDs should light up.
#
#                 If you get random colors across your LEDs, change the color_order to GRB and restart. Then
#                 omit the W for each suggested color_order in the next paragraph.
#
#                 If you get MAGENTA, your  color order is correct. If you get CYAN, you need to use RGBW. If
#                 you get YELLOW, you need to use BRGW (note that BRG is only supported in the latest Klipper
#                 version).
#
#     4.  Once you have confirmed that the LEDs are set up correctly, you must now decide where you want 
#         these macros called up...which means adding them to your existing gcode macros.  NOTHING will happen
#         unless you add the STATUS_????? macros to your existing gcode macros.  
#
#           Example: add STATUS_LEVELING to the beginning of your QGL gcode macro, and then add STATUS_READY 
#                    to the end of it to set the logo LED and nozzle LEDs back to the `ready` state.
#
#           Example: add STATUS_CLEANING to the beginning of your nozzle-cleaning macro, and then STATUS_READY
#                    to the end of it to return the LEDs back to `ready` state.
#
#     5.  Feel free to change colors of each macro, create new ones if you have a need to.  The macros provided below
#         are just an example of what is possible.  If you want to try some more complex animations, you will most
#         likely have to use WLED with Moonraker and a small micro-controller 
#
#####################################
#       END INSTRUCTRUCTIONS        #
#####################################


[neopixel sb_leds]
pin: EBBCan:gpio16
#   The pin connected to the neopixel. This parameter must be provided.
chain_count: 10
#   The number of Neopixel chips that are "daisy chained" to the
#   provided pin. The default is 1 (which indicates only a single
#   Neopixel is connected to the pin).
color_order: GRB,GRB,GRB,GRB,GRB,GRB,GRB,GRB,GRBW,GRBW
#   Set the pixel order required by the LED hardware. Options are GRB,
#   RGB, GRBW, or RGBW. The default is GRB.
initial_RED: 1.0
initial_GREEN: 0.45
initial_BLUE: 0.0
initial_WHITE: 1.0
#   Sets the initial LED color of the Neopixel. Each value should be
#   between 0.0 and 1.0. The WHITE option is only available on RGBW
#   LEDs. The default for each color is 0.#

# Most configuration for the macros can be done by modifying the variables in the _sb_vars macro
# at the start of this file.

##########
# MACROS #
##########

# The following status macros are available (these go inside of your macros):
#
#    STATUS_READY
#    STATUS_OFF
#    STATUS_BUSY
#    STATUS_HEATING
#    STATUS_LEVELING
#    STATUS_HOMING
#    STATUS_CLEANING
#    STATUS_MESHING
#    STATUS_CALIBRATING_Z
#
# With additional macros for basic control:
#
#    SET_NOZZLE_LEDS_ON
#    SET_LOGO_LEDS_OFF
#    SET_NOZZLE_LEDS_OFF
#
# Contributed by Voron discord users wile.e, Tetsunosuke, and etherwalker


[gcode_macro _sb_vars]
# User settings for the StealthBurner status leds. You can change the status colors and led
# configurations for the logo and nozzle here.
variable_colors: {
        'logo': { # Colors for logo states
            'busy': {'r': 0.4, 'g': 0.0, 'b': 0.0, 'w': 0.0},
            'cleaning': {'r': 0.0, 'g': 0.02, 'b': 0.5, 'w': 0.0},
            'calibrating_z': {'r': 0.8, 'g': 0., 'b': 0.35, 'w': 0.0},
            'heating': {'r': 0.3, 'g': 0.18, 'b': 0.0, 'w': 0.0},
            'homing': {'r': 0.0, 'g': 0.6, 'b': 0.2, 'w': 0.0},
            'leveling': {'r': 0.5, 'g': 0.1, 'b': 0.4, 'w': 0.0},
            'meshing': {'r': 0.2, 'g': 1.0, 'b': 0.0, 'w': 0.0},
            'off': {'r': 0.0, 'g': 0.0, 'b': 0.0, 'w': 0.0},
            'printing': {'r': 1.0, 'g': 0.0, 'b': 0.0, 'w': 0.0},
            'standby': {'r': 0.00, 'g': 0.5, 'b': 0.5, 'w': 0.0},
        },
        'nozzle': { # Colors for nozzle states
            'heating': {'r': 0.8, 'g': 0.35, 'b': 0.0, 'w':0.0},
            'off': {'r': 0.0, 'g': 0.0, 'b': 0.0, 'w': 0.0},
            'on': {'r': 0.8, 'g': 0.8, 'b': 0.8, 'w':1.0},
            'standby': {'r': 0.0, 'g': 0.0, 'b': 0.0, 'w':0.0},
        },
        'thermal': {
            'hot': {'r': 1.0, 'g': 0.0, 'b': 0.0, 'w': 0.0},
            'cold': {'r': 0.3, 'g': 0.0, 'b': 0.3, 'w': 0.0}
        }
    }
variable_logo_led_name:         "sb_leds" 
# The name of the addressable LED chain that contains the logo LED(s)
variable_logo_idx:              "1" 
# A comma-separated list of indexes LEDs in the logo
variable_nozzle_led_name:       "sb_leds"
# The name of the addressable LED chain that contains the nozzle LED(s). This will
# typically be the same LED chain as the logo.
variable_nozzle_idx:            "2,3"
# A comma-separated list of indexes of LEDs in the nozzle
gcode:
    # This section is required.  Do Not Delete.


[gcode_macro _set_sb_leds]
gcode:
    {% set red = params.RED|default(0)|float %}
    {% set green = params.GREEN|default(0)|float %}
    {% set blue = params.BLUE|default(0)|float %}
    {% set white = params.WHITE|default(0)|float %}
    {% set led = params.LED|string %}
    {% set idx = (params.IDX|string).split(',') %}
    {% set transmit_last = params.TRANSMIT|default(1) %}

    {% for led_index in idx %}
        {% set transmit=transmit_last if loop.last else 0 %}
        set_led led={led} red={red} green={green} blue={blue} white={white} index={led_index} transmit={transmit}
    {% endfor %}

[gcode_macro _set_sb_leds_by_name]
gcode:
    {% set leds_name = params.LEDS %}
    {% set color_name = params.COLOR %}
    {% set color = printer["gcode_macro _sb_vars"].colors[leds_name][color_name] %}
    {% set led = printer["gcode_macro _sb_vars"][leds_name + "_led_name"] %}
    {% set idx = printer["gcode_macro _sb_vars"][leds_name + "_idx"] %}
    {% set transmit = params.TRANSMIT|default(1) %}

    _set_sb_leds led={led} red={color.r} green={color.g} blue={color.b} white={color.w} idx="{idx}" transmit={transmit}

[gcode_macro _set_logo_leds]
gcode:
    {% set red = params.RED|default(0)|float %}
    {% set green = params.GREEN|default(0)|float %}
    {% set blue = params.BLUE|default(0)|float %}
    {% set white = params.WHITE|default(0)|float %}
    {% set led = printer["gcode_macro _sb_vars"].logo_led_name %}
    {% set idx = printer["gcode_macro _sb_vars"].logo_idx %}
    {% set transmit=params.TRANSMIT|default(1) %}

    _set_sb_leds led={led} red={red} green={green} blue={blue} white={white} idx="{idx}" transmit={transmit}

[gcode_macro _set_nozzle_leds]
gcode:
    {% set red = params.RED|default(0)|float %}
    {% set green = params.GREEN|default(0)|float %}
    {% set blue = params.BLUE|default(0)|float %}
    {% set white = params.WHITE|default(0)|float %}
    {% set led = printer["gcode_macro _sb_vars"].nozzle_led_name %}
    {% set idx = printer["gcode_macro _sb_vars"].nozzle_idx %}
    {% set transmit=params.TRANSMIT|default(1) %}

    _set_sb_leds led={led} red={red} green={green} blue={blue} white={white} idx="{idx}" transmit={transmit}

[gcode_macro set_logo_leds_off]
gcode:
    {% set transmit=params.TRANSMIT|default(1) %}
    _set_logo_leds red=0 blue=0 green=0 white=0 transmit={transmit}

[gcode_macro set_nozzle_leds_on]
gcode:
    {% set transmit=params.TRANSMIT|default(1) %}
    _set_sb_leds_by_name leds="nozzle" color="on" transmit={transmit}
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
